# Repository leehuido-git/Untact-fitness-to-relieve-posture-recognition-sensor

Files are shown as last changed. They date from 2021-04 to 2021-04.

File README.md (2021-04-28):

# Untact-fitness-to-relieve-posture-recognition-sensor
Using the MPU-9250 IMU sensor, get the angle of a part of the body and visualize it with Unity or implement the arm shape using the RX-64.
여러개의 MPU-9250 IMU를 통해서 각 신체부위의 quaternion값을 받아 Unity로 시각화, 여러개의 RX-64를 통해서 팔을 구현.

목차
1. [Directory](#Directory)
2. [동기](#동기)
3. [개요](#개요)
4. [Block diagram](#Block-diagram)
5. [Flow chart](#Flow-chart)
6. [Circuit](#Circuit)
7. [Result](#Result)
8. [느낀점](#느낀점)

## Directory
```
.
├── circuit/
    ├── master/
    ├── Robot_Arm/
    ├── slave/
├── datasheet/
├── doc/
    ├── RX-64_정리.hwp
    ├── 중간보고서.hwp
    ├── 결과보고서.hwp
├── img/
├── Modeling/
    ├── stress_calculation/
├── source/
    ├── master/
    ├── Robot_Arm/
    ├── slave/
└── Unity/
```

각각의 것들에 대한 개요입니다:

| 파일 | 설명 |
| --- | --- |
| `RX-64_정리.hwp` | RX-64를 사용하기 위한 스펙, 프로토콜등을 정리 |
| `중간보고서.hwp` | 캡스톤디자인 중간보고서 |
| `결과보고서.hwp` | 캡스톤디자인 결과보고서이며 더 궁금한 내용은 여기를 참조 |
| `master/` | IMU Master를 위한 Arduino 소스 |
| `slave/` | IMU Slave를 위한 Arduino 소스 |
| `Robot_Arm/` | RX-64를 제어하기 위한 Atmel 소스 |

## 동기
1. COVID-19로 인해 비대면  서비스가  증가하는 반면 COVID-19 검체 현장에서는 대면접촉이  이루어 지고 있어 의료관계자들은 감염 위험에 노출되어 있습니다. 또한, 여름에 레벨D 방호복을 입으면 땀 닦을 수도, 물도 마실 수 없어 피부병도 빈번하게 발생하며, 내부 온도는 38도에 육박했다. 그렇기에 저희는 원격으로 COVID-19의 검체를 진행할 수 있다면 이러한 감염위험이나 의료관계자의 불편함을 줄일 수 있을 것입니다. 또한 검체를 채취하는 과정에서 일회용 보호복을 사용하는 경우가 많은데 원격으로 진행할 수 있다면 그 비용을 절약할 수 있을 것입니다.

2. 헬스장의 기존의 대면식 PT를 대체할 비대면식 PT를 제공하며 복잡한 회원 관리가 없어져 일반 헬스장, 아파트 헬스장등 기존 회원 관리의 문제점을 타파할 수 있으며 운동관련 인플루언서들은 자신의 운동을 등록하여 기존의 플랫폼의 단순 동영상 시청의 컨텐츠가 아닌 실제 자신의 운동방식을 알릴 수 있습니다.

## 개요
본 시스템은 크게 4가지 단계로 이루어져 있습니다. (팔 기준)
1. IMU Slave
IMU Slave를 손등, 아래팔, 위팔에 달아주며, 플렉스 센서가 붙여진 장갑을 끼면 각 IMU의 quaternion값, 각 손의 플렉스 센서값을 Wi-Fi를 통해서 IMU Master에게 보내줍니다.
    ```
	동작 알고리즘    
	1. IMU Master으로부터 보정값 받을 때까지 대기한다.
	2. 보정값을 받으면 MPU-9250을 통해 보정된 Quaternion값을 받는다.
    3. Flexible sensor값들을 받는다.
	4. Quaternion값, IMU_2의 이름, Flexible sensor값들을 함께 Wi-Fi를 통해 IMU_MAIN에 전송한다.
    ```

2. IMU Master
초기 IMU Slave가 구동할 때 ACC, MAG, GYRO의 보정값을 IMU Slave에게 보내게 되며, IMU Slave에게 받은 값을 Unity에는 quaternion값을 보내게 되며, Atmega에는 변환된 Euler Angle과 플렉스 센서값을 보내게 됩니다.
    ```
	동작 알고리즘
	1. ACC, MAG, GYRO를 각각 두 번 보정하여 평균값을 계산한다.
	2. Wi-Fi를 통해 5초동안 IMU_1, IMU_2에 보정값 전송한다.
	3. IMU_1, IMU_2...에서 받는 순서대로 Quaternion값을 UART0에 전송한다.
	4. IMU_1, IMU_2에서 받는 순서대로 Quaternion값을 Euler Angle로 계산하고, Flexible sensor값과 함께 UART1을 통해 ATmega에 전송한다.
    ```

3. Atmega-128A(RX-64)
초기 Euler Angle값을 init하여 이후에 변환하는 Euler Angle을 Denavit–Hartenberg parameters를 통해 RX-64에 모터각 전송합니다.
    ```
	동작 알고리즘
	1. IMU_MAIN으로부터 Euler Angle값, Flexible sensor값 받을 때까지 대기한다.
	2. Euler Angle값을 출력하며, 지정된 자세일 때 Button을 눌러 init,
	3. init한 Euler Angle값과의 상대 Euler Angle값을 계산한다.
	4. 상대 Euler Angle값을 Denavit–Hartenberg parameters를 통해 각 motor Angle 계산한다.
	5. Timer를 통해 50ms를 주기로 RX-64에 데이터 전송한다.
	6. Flexible sensor값을 0~180도로 나누어 servomotor PWM 제어한다.
    ```

4. Unity
받은 quaternion값을 통해서 초기 Quaternion값을 init하여 이후에 변환하는 상대 Quaternion값을 계산하여 Bone을 제어합니다.
    ```
	동작 알고리즘
	1. UART를 사용할 PORT 설정 및 연다.
	2. IMU_MAIN으로부터 Quaternion값 받을 때까지 대기한다.
	3. Quaternion값을 출력하며, 지정된 자세일 때 spacebar를 눌러 init.
	4. init한 Quaternion값과의 상대 Quaternion값을 계산한다.
	5. Bone제어한다.
    ```

## Block diagram
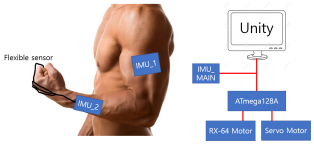
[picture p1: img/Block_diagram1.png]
Block_diagram1
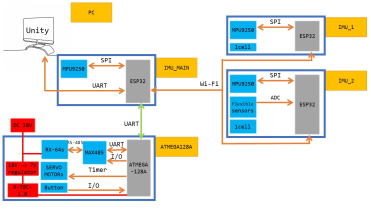
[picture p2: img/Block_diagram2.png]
Block_diagram2
 
* 부하가 많이 발생하여 RX-64 maximun voltage에 근접하는 18v인가
* R-78C 5.0-1.0을 통해서 atmega128A recommended voltage인 5v로 switching regulation
* RX-64는 RS-485통신을 사용하므로 max485를 통해서 RS-232(UART)를 RS-485로 변환
* Atmega와 IMU간 UART 송수신
* Computer와 IMU간 UART 송수신
* IMU인 MPU-9250과 MCU인 ESP32간 I2C, SPI통신을 사용할 수 있는데 빠른 SPI통신 사용(I2C at 400kHz or SPI at 1MHz)
* IMU Slave는 배터리 1cell을 사용, 통신은 Wi-Fi을 사용하여 무선으로 사용 가능

## Flow chart
**1. IMU Master flow chart**  
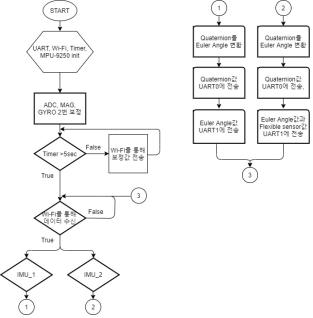
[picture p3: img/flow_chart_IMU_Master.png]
flow_chart_IMU_Master
  

**2. IMU Slave flow chart**  
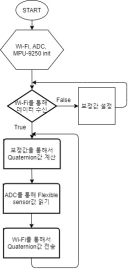
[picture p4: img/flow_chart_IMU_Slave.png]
flow_chart_IMU_Slave


**3. Atmega flow chart**  
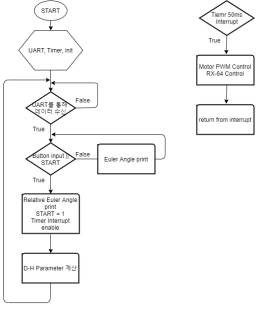
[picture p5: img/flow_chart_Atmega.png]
flow_chart_Atmega


## Circuit
**1. IMU Master Circuit**  
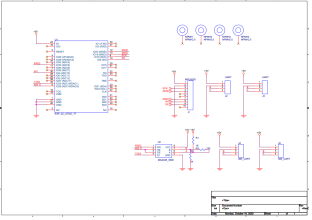
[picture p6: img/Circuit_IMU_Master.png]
Circuit_IMU_Master
  

**2. IMU Slave Circuit**  
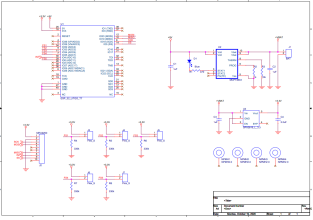
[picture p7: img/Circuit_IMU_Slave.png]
Circuit_IMU_Slave


**3. Atmega Circuit**  
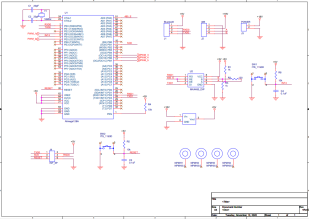
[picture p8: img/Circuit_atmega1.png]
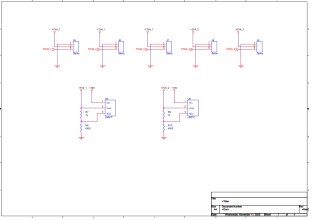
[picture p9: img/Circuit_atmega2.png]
 

## Result
result1  
실제 프로토타입으로 개발하였던 센서를 기반으로 atmega와 연동하여 RX-64를 구동하는 것을 보여줍니다.

result2  
실제 프로토타입으로 개발하였던 센서를 기반으로 Unity와 연동하여 스마트미러를 통해 데이터를 받아오는 것을 보여줍니다.

## 느낀점
1. 현재 COVID-19가 창궐하면서 언택트 시대에서 온택트 시대로 넘어가고 있습니다. 온택트 시대는 온라인을 통해 대면을 하는 것으로 소비자들의 간접적 경험을 심어줄 수 있는 체험 미디어가 있느냐 없느냐인데, 저희가 만든 로봇팔과 같이 소비자에게 행동을 보여줌으로써 간접적 경험을 심어줄 수 있습니다. 또한 이뿐만 아니라 공장 내 작업자의 협동로봇 간편 티칭으로도 사용할 수 있습니다. 4차 산업혁명의 주요 과제로 근로자와 함께 근로공간을 공유하여 사용하는 사례가 많은데 협동로봇을 제어에는 전문가가 투입되지만 본 솔루션을 통해 작업자의 신체에 센서를 부착하여 원격으로 작업을 수행할 수 있을 것입니다.
2. IMU를 통해서 로봇 팔을 제작, 제어하는데에는 많은 분야의 지식이 필요하고 생각보다 잘 안된게 아쉽습니다.
3. 로봇 팔의 모터를 더 강력한 모터를 사용, 모터를 추가하여 자유도를 높이고 싶지만 자원의 제약으로 사용하지 못하는게 아쉽습니다.
4. Magwick Filter와 보정을 모두 했지만 오차가 존재하며 특히 Yaw값의 누적오차가 발생했습니다.
4. 생각외로 servomotor는 전류소모가 매우 크다는 것을 알게 되었습니다.

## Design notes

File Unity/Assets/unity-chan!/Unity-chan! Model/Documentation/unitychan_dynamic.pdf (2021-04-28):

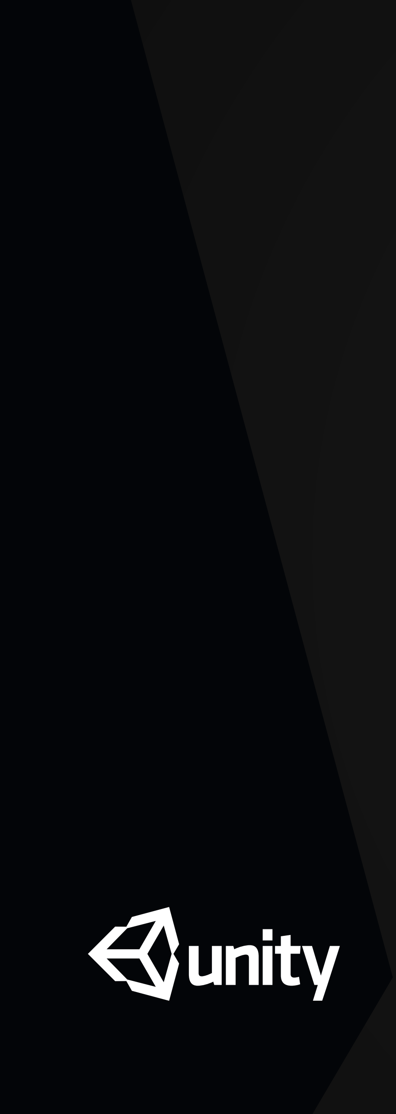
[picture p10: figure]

# ダイナミック版ユニティちゃん （unitychan_dynamic） マニュアル

# Unity4.3.4以上対応

2014/07/23

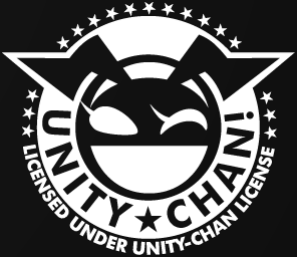
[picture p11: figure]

# 『ダイナミック版ユニティちゃん』とは

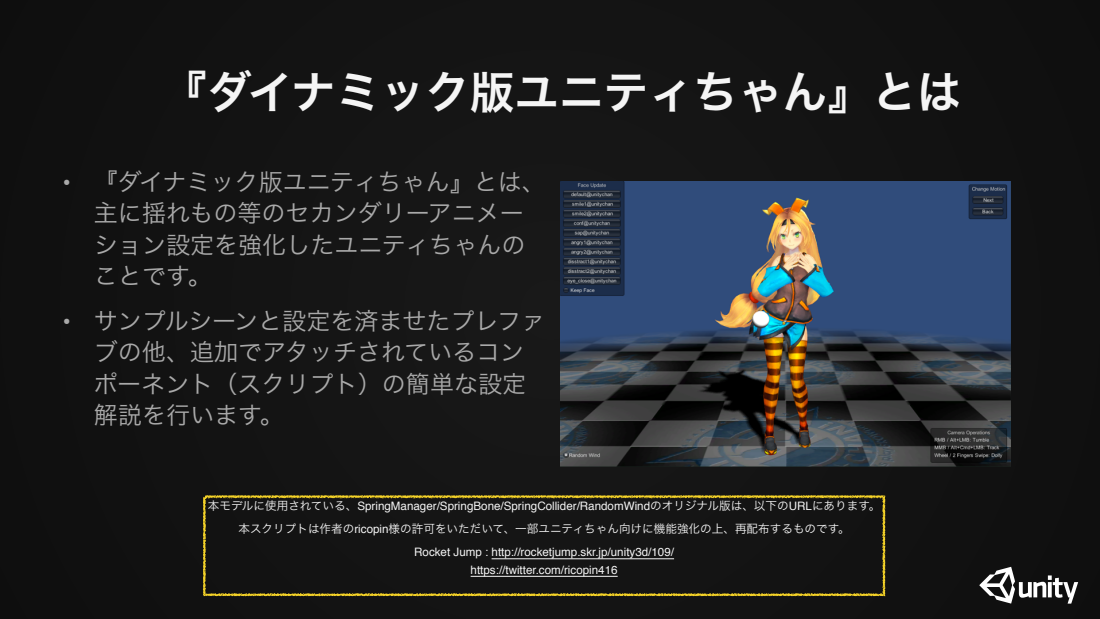
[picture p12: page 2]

• 『ダイナミック版ユニティちゃん』とは、
主に揺れもの等のセカンダリーアニメー
ション設定を強化したユニティちゃんの
ことです。
• サンプルシーンと設定を済ませたプレファ
ブの他、追加でアタッチされているコン
ポーネント（スクリプト）の簡単な設定
解説を行います。

本モデルに使用されている、SpringManager/SpringBone/SpringCollider/RandomWindのオリジナル版は、以下のURLにあります。

本スクリプトは作者のricopin様の許可をいただいて、一部ユニティちゃん向けに機能強化の上、再配布するものです。

Rocket Jump : http://rocketjump.skr.jp/unity3d/109/

https://twitter.com/ricopin416

# サンプルシーン SecondaryAnimation Locomotion

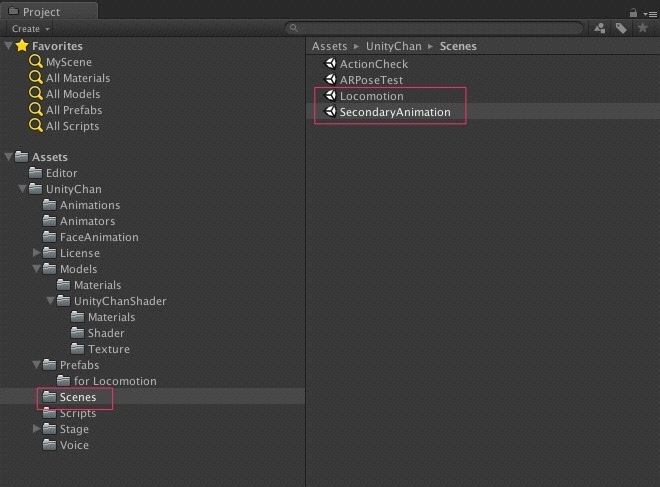
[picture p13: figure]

### - Assets>UnityChan>Scenes中の 「SecondaryAnimation」と「Locomotion」がサ ンプルシーンになります。

### - SecondaryAnimationは、ポージングやダンス モーションなど、ユニティちゃんが原点の付近で あまり動かない場合のセッティング例です。見栄 え優先で揺れ物を揺らすセッティングになってい

ます。

### - Locomotionは、ユニティちゃんを PlayerControllerなどで動かす場合のセッティン グ例です。揺れ物のセッティングが少し固めになっ ています。

### - 各シーンを開くことで、すぐにダイナミック設定 のついたユニティちゃんで遊ぶことができます。

# プレファブ unitychan_dynamic unitychan_dynamic_locomotion

### - Prefabsフォルダ内には、サンプルシーンで使用されて

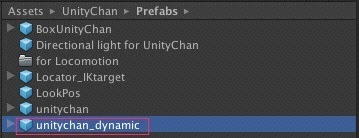
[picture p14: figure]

### いるダイナミック版ユニティちゃんのプレファブが入っ ています。

### - Assets>UnityChan>Prefabs unitychan_dynamic →SecondaryAnimationシーン用プレファブ

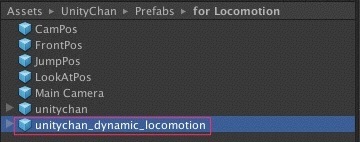
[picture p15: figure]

### - Assets>UnityChan>Prefabs>for Locomotion unitychan_dynamic_locomotion →Locomotionシーン用プレファブ

### - これらのプレファブを自分の好きなシーンに配置する ことで、各ダイナミック用設定を済ませたユニティちゃ んをすぐに使うことができるようになります。

# 『ダイナミック版ユニティちゃん』の 揺れ物制御用コンポーネントについて

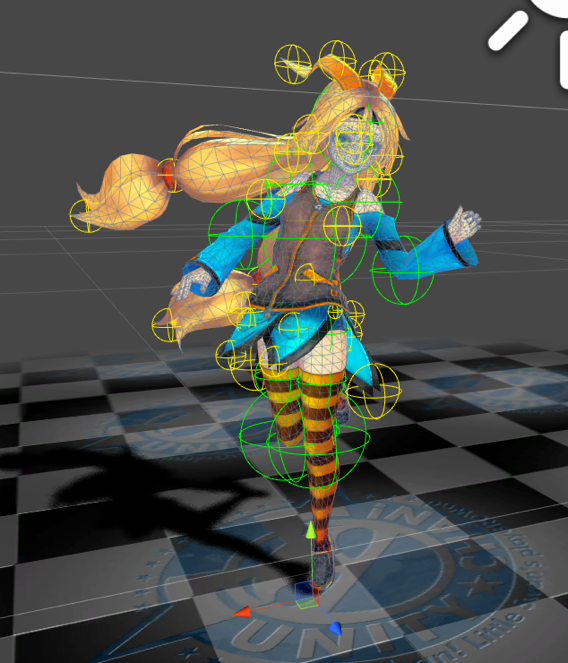
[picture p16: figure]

- 『ダイナミック版ユニティちゃん』の揺れ物制御用のコンポーネントは以 下のような構成になっています。
- SpringManager.cs：SpringBoneを制御するマネージャー。ユニティちゃ ん本体にアタッチされる。
- SpringBone.cs：各揺れ物用ボーンにアタッチされるコンポーネント。揺 れ物に設定されている各ボーン（ジョイント）にアタッチされる
- SpringCollider.cs：SpringBone専用の当たり判定用コライダー。当たり判 定を付けたいジョイントやロケータにアタッチされる。
- RandomWind.cs：ランダムに風にそよぐような効果を生み出すコンポー ネント。ユニティちゃん本体にアタッチされる。ゲームビュー内の 「Random Wind」で機能をON/OFFできる。
- CreateLocatorHere.cs：SpringCollider設定支援用エディタ拡張ツール。 Hierarchy上であるジョイントを指定して実行することで、そのジョイント の子の位置にロケータを生成できる。ロケータは親のジョイントからロー カル移動をすることで、位置をオフセットすることができる。生成したロ ケータにはSpringCollider.csをアタッチする。

# 『ダイナミック版ユニティちゃん』に 追加されたその他のコンポーネント について

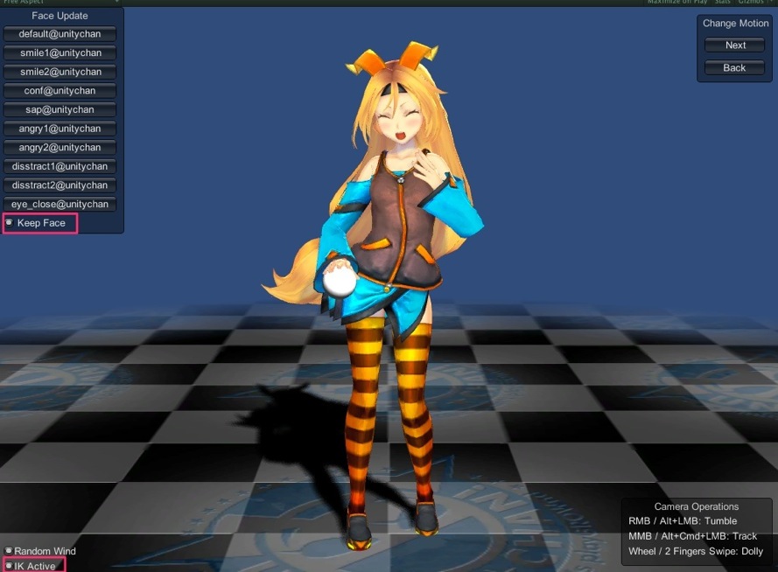
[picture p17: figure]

- AutoBlink.cs：自動で目パチアニメーションをさせ るコンポーネント。
- FaceUpdate.cs：機能強化版。表情の固定ができる ようになった（KeepFaceをチェック後、表情スイッ チを押す）他、Mecanimアニメーションイベント
で、OnCallFaceChange(“表情名”)を呼び出すこと で、各アニメーションデータ上で、タイムラインに
沿って表情変化を設定できます。
- IKCtrlRightHand.cs：Pro Onlyの機能。右手のIKコ ントロールのサンプルです。コンポーネントを有効
にした後、ゲームビュー内の「IK Active」でON/OFF できます。

# SpringBone.csの設定①

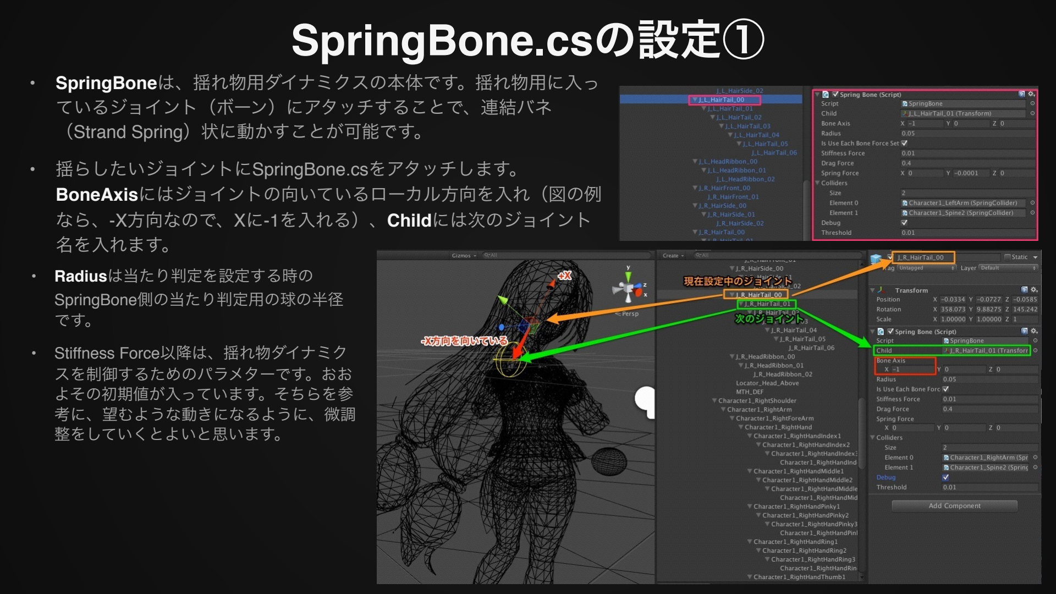
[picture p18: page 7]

### - SpringBoneは、揺れ物用ダイナミクスの本体です。揺れ物用に入っ ているジョイント（ボーン）にアタッチすることで、連結バネ （Strand Spring）状に動かすことが可能です。

### - 揺らしたいジョイントにSpringBone.csをアタッチします。 BoneAxisにはジョイントの向いているローカル方向を入れ（図の例 なら、-X方向なので、Xに-1を入れる）、Childには次のジョイント 名を入れます。

- Radiusは当たり判定を設定する時の
SpringBone側の当たり判定用の球の半径
です。
- Stiffness Force以降は、揺れ物ダイナミク スを制御するためのパラメターです。おお
よその初期値が入っています。そちらを参
考に、望むような動きになるように、微調
整をしていくとよいと思います。

# SpringBone.csの設定②

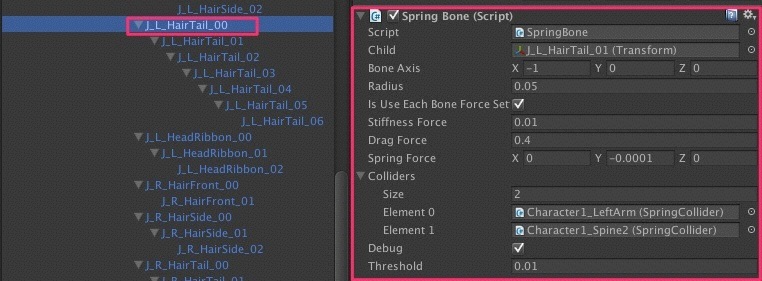
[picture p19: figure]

- StiffnessForce、DragForceはそれぞれ「バネが戻るフォース」「フォースの 減衰力」です。後に説明しますが、IsUseEachBoneForceSetにチェックが 入っている時には、SpringBone側に設定されているこれらのパラメターが使用 されます。
- Collidersには、各SpringBoneコンポーネントと当たり判定を設定したい SpringColliderを設定します。
- 最後にThresholdは、このSpringBoneコンポーネントを制御している SpringManager側のDynamicRatioが有効になる最低値を設定します。（この値 を上げることで、一部のSpringBoneを個別に停止して、揺れ物ボーンに元々つ いているアニメーションに切り替えることが可能になります。）
- SpringBoneの設定で重要なのは、①でのChild/BoneAxis/Radiusの設定と、②の Collidersの設定です。その他の値は、初期値を参考に微調整をするとよいで しょう。
- SpringBoneの効き具合の調整は、上のStiffnessForce/DragForceの値で微調 整をする他に、後述するSpringManager側のDynamicRatioで効果自体の効き 具合を調整してしまうという方法があります。大体の設定が終わった後は、 DynamicRatio側で使う状況に合わせて調整するほうが便利なようです。

# SpringManager.csの設定

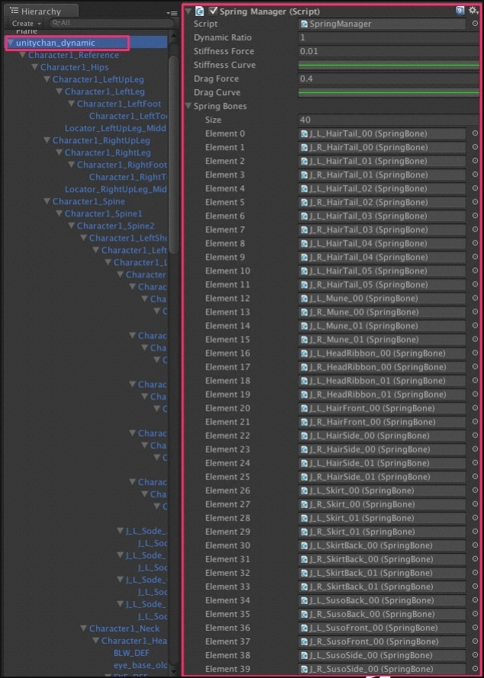
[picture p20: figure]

- SpringManagerは、配下にあるSpringBoneを制御するコンポーネントです。
- SpringBones以下に管理させたいSpringBoneがアタッチされているジョイントを必ず親 から順に指定します。
- DynamicRatioは、配下にあるSpringBoneの影響の強さを制御するパラメターです。 DynamicRatio=1の時、SpringBoneの影響が最大になり、DynamicRatio=0の時、 SpringBoneの機能はキャンセルされます。その場合、ジョイントが持っている元々の ローカルローテーション値もしくは、揺れ物ボーンに付けられているアニメーションで のローテーション値が使用されます。DynamicRatioは、各SpringBoneに設定できる Thresholdを参照できますので、各SpringBoneのThresholdを適宜設定し、DynamicRatio を調整することで、一部の揺れ物ボーンは、元々のアニメーションで、一部の揺れ物ボー ンはSpringBoneで動かすというようなことも可能です。
- SpringManager側にあるStiffnessForceとDragForceは、配下にあるSpringBoneの同名の 値の最適値を探るために使えます。有効にする場合には、各SpringBoneの IsUseEachBoneForceSetがオフになっている必要があります。カーブなどを利用して 様々な設定のパターンを探ることができるようになっています。SpringManager上でシ ミュレーションした値は、エディタ上でしか使えませんので、よい値が見つかったら SpringBone側に値をコピーし、IsUseEachBoneForceSetをチェックすることをお薦めし ます。
- なおSpringManagerは、各揺れ物ボーンのチェインの一番上の階層に付けることで、各 揺れ物ボーンのチェインを個別に管理することも可能です。

# SpringCollider.csの設定

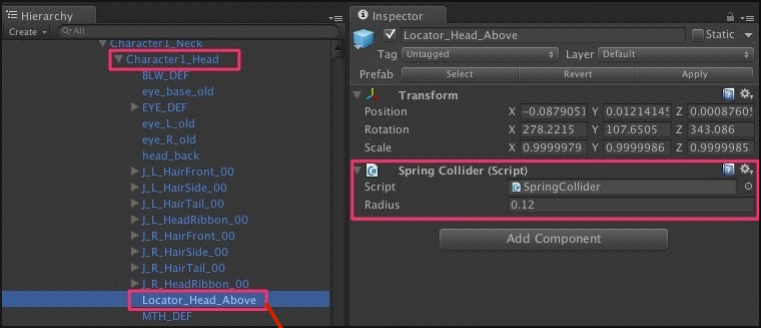
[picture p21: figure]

- SpringColliderは、SpringBoneコンポーネントと衝突判定を行うためのコンポーネン トです。ジョイントやジョイントからオフセットした位置に設定したロケータにアタッ チすることで、当たり判定用のスフィアコライダーとして利用することができます。 Radiusが当たり判定用のスフィアコライダーの半径となります。
- 当たり判定をとりたいSpringBoneコンポーネント側の配列（Colliders）に、判定し たいSpringColliderをアタッチしたオブジェクト名を指定します。
- エディタ拡張コマンドCreateLocatorHere.csを使うことで、Hierarchy上でジョイント の子の位置にロケータを生成できます。ロケータは親のジョイントからローカル移動を することで、位置をオフセットすることができますので、オフセットした位置で SpringColliderを複数設定することで、複雑な当たり判定領域を設定したり、ジョイン トから離れている位置に当たり判定領域を設定することができます。 CreateLocatorHereは、Hierarchy上でジョイントを選んだ後、GameObjectメニューか らコマンド選択する他、Transformコンポーネント上で右クリックメニューから呼び出 すことで利用できます。

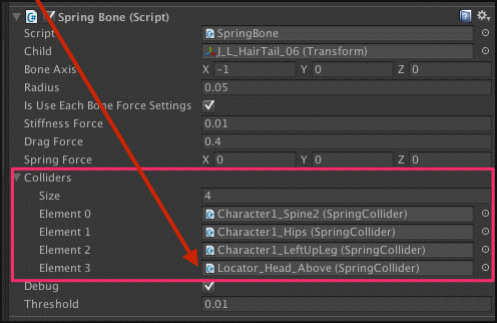
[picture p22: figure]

- SpringColliderはUnity標準の物理エンジンによる当たり判定を使用していませんので、 ご注意ください。

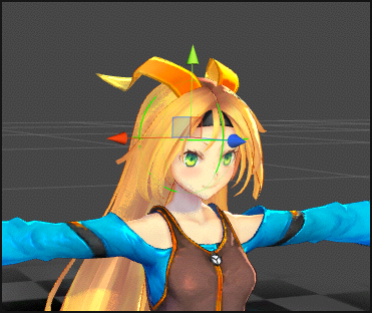
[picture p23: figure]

# FaceUpdate.cs / OnCallFaceChangeの設定

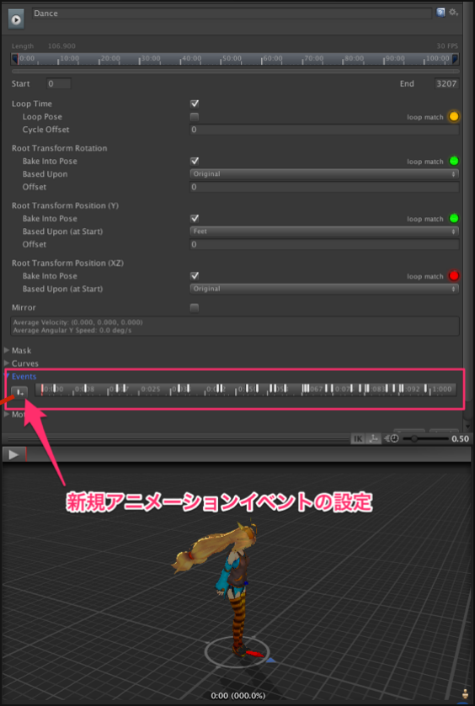
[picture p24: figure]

- FaceUpdate.cs：機能強化版。表情の固定ができるようになった （KeepFaceをチェック後、表情スイッチを押す）他、Mecanimアニメー ションイベントで、OnCallFaceChange(“表情名”)を呼び出すことで、各ア ニメーションデータ上で、タイムラインに沿って表情変化を設定できます。
- ダンスモーションなどのアニメーションデータをMecanimで開き、Events タブを開いて、モーションに合わせて新規アニメーションイベントを設定し ます。
- Edit AnimationEventウィンドウが開きますので、Functionに 「OnCallChangeFace」と入れ、Stringに「変更したいフェイスの名前」を 指定します。

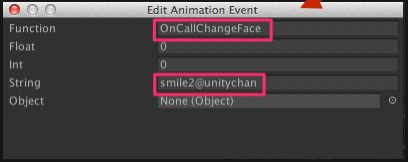
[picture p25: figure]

# FaceUpdate.cs / 新規表情の追加

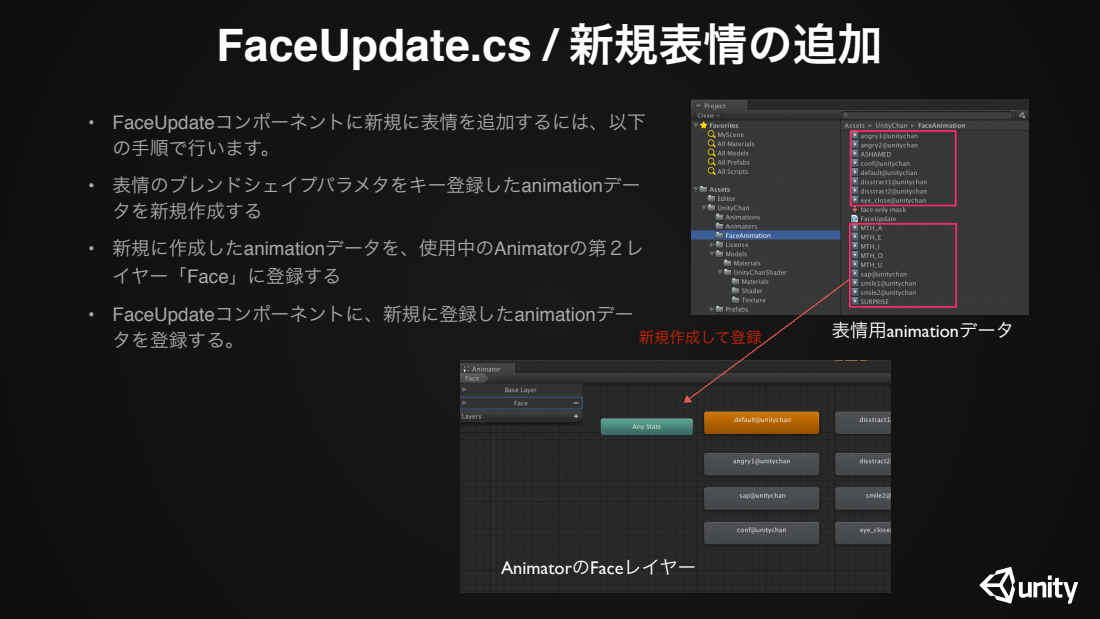
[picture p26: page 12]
• FaceUpdateコンポーネントに新規に表情を追加するには、以下 の手順で行います。; • 表情のブレンドシェイプパラメタをキー登録したanimationデー タを新規作成する; • FaceUpdateコンポーネントに、新規に登録したanimationデー; タを登録する。; 表情用animationデータ; AnimatorのFaceレイヤー; 新規作成して登録

• 新規に作成したanimationデータを、使用中のAnimatorの第２レ
イヤー「Face」に登録する

# 表情アニメーションデータの新規作成

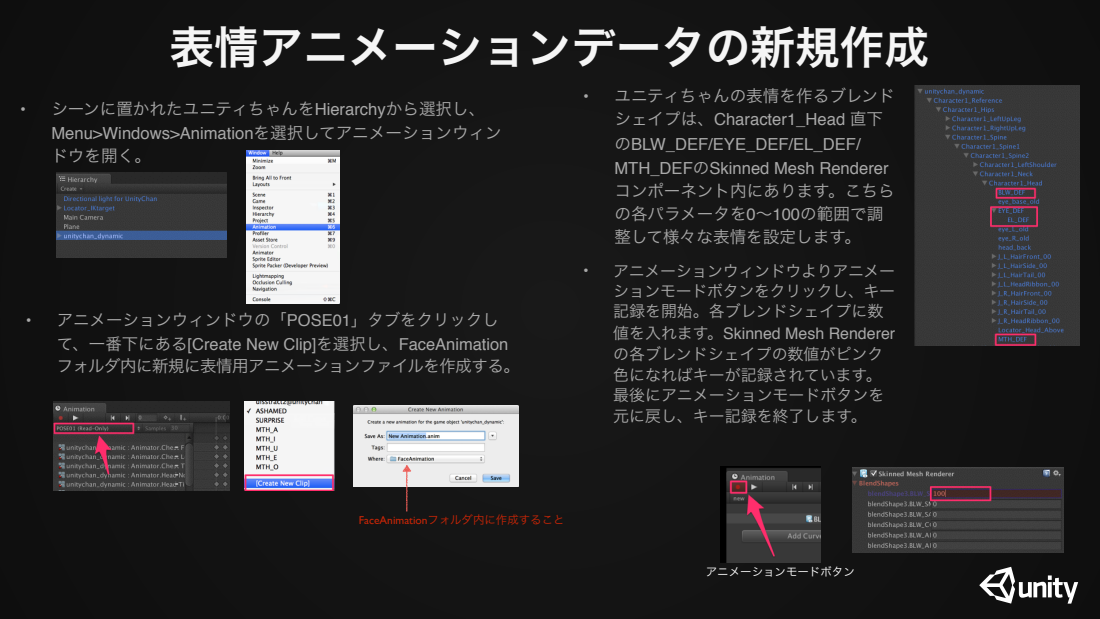
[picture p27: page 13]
• ユニティちゃんの表情を作るブレンド シェイプは、Character1_Head 直下 のBLW_DEF/EYE_DEF/EL_DEF/ MTH_DEFのSkinned Mesh Renderer コンポーネント内にあります。こちら の各パラメータを0～100の範囲で調 整して様々な表情を設定します。; アニメーションモードボタン; FaceAnimationフォルダ内に作成すること

• シーンに置かれたユニティちゃんをHierarchyから選択し、
Menu>Windows>Animationを選択してアニメーションウィン
ドウを開く。

• アニメーションウィンドウよりアニメー
ションモードボタンをクリックし、キー
記録を開始。各ブレンドシェイプに数
値を入れます。Skinned Mesh Renderer
の各ブレンドシェイプの数値がピンク
色になればキーが記録されています。
最後にアニメーションモードボタンを
元に戻し、キー記録を終了します。

• アニメーションウィンドウの「POSE01」タブをクリックし
て、一番下にある[Create New Clip]を選択し、FaceAnimation
フォルダ内に新規に表情用アニメーションファイルを作成する。

# 表情アニメーションデータの登録

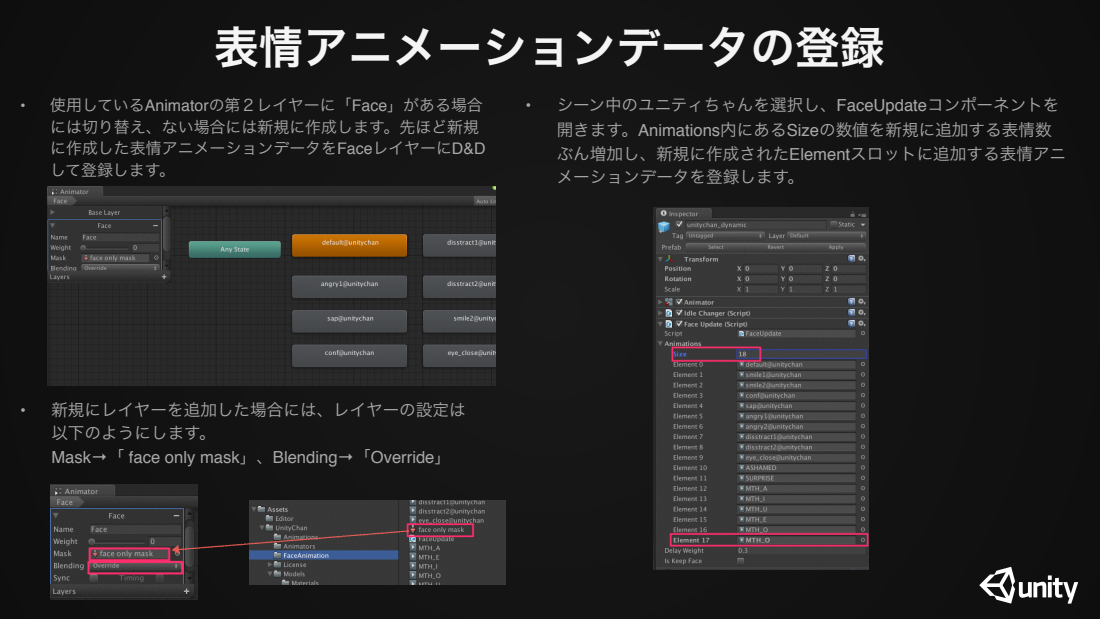
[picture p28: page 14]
• シーン中のユニティちゃんを選択し、FaceUpdateコンポーネントを 開きます。Animations内にあるSizeの数値を新規に追加する表情数 ぶん増加し、新規に作成されたElementスロットに追加する表情アニ メーションデータを登録します。

• 使用しているAnimatorの第２レイヤーに「Face」がある場合
には切り替え、ない場合には新規に作成します。先ほど新規
に作成した表情アニメーションデータをFaceレイヤーにD&D
して登録します。

• 新規にレイヤーを追加した場合には、レイヤーの設定は
以下のようにします。
Mask→「 face only mask」、Blending→「Override」

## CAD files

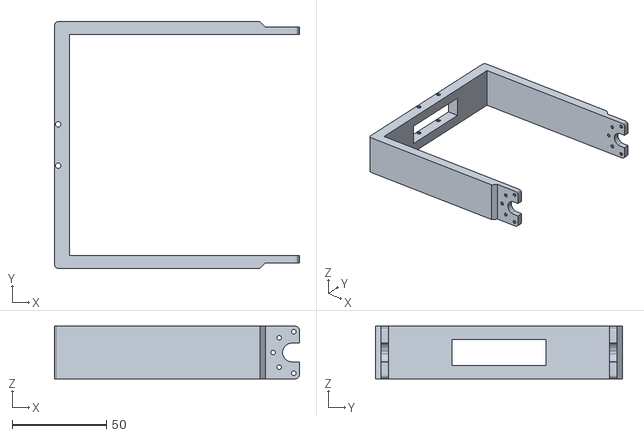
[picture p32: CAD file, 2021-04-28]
Modeling/shoulder_gear.stl
130.0 x 131.0 x 28.0

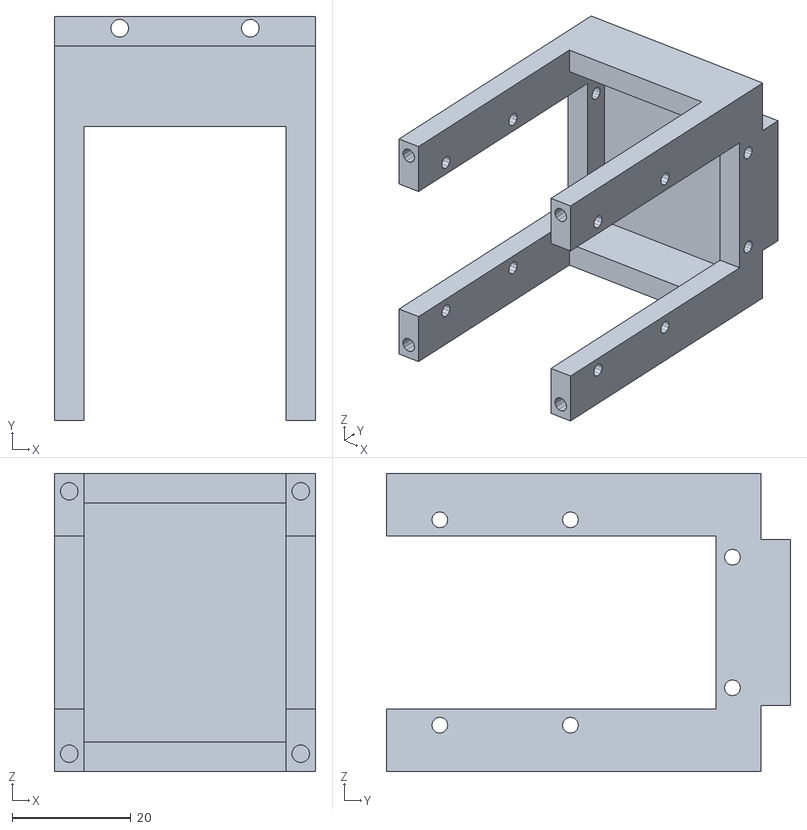
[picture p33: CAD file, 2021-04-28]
Modeling/elbow.stl
44.0 x 68.1 x 50.2

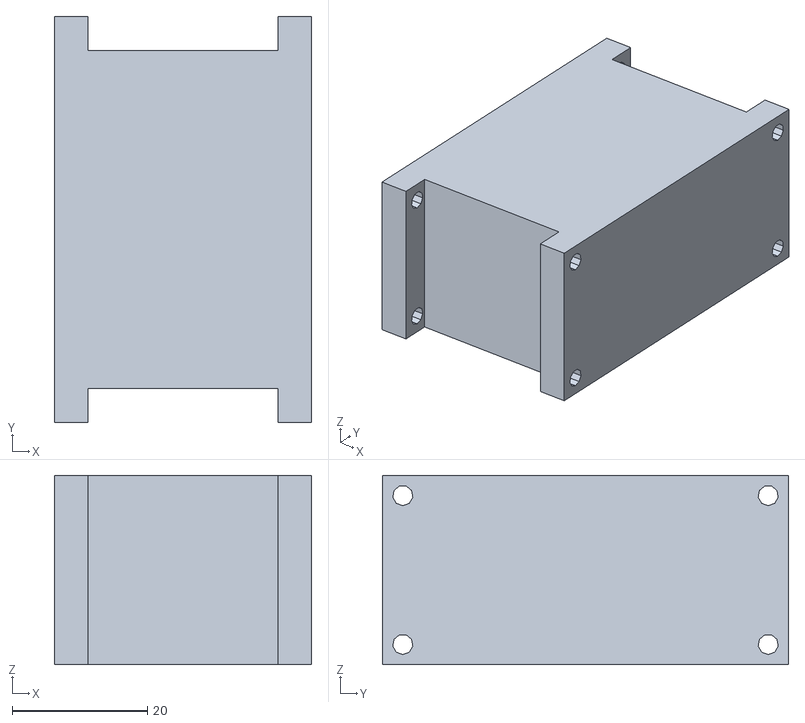
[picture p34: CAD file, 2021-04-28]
Modeling/upperarm.stl
38.0 x 60.0 x 28.0

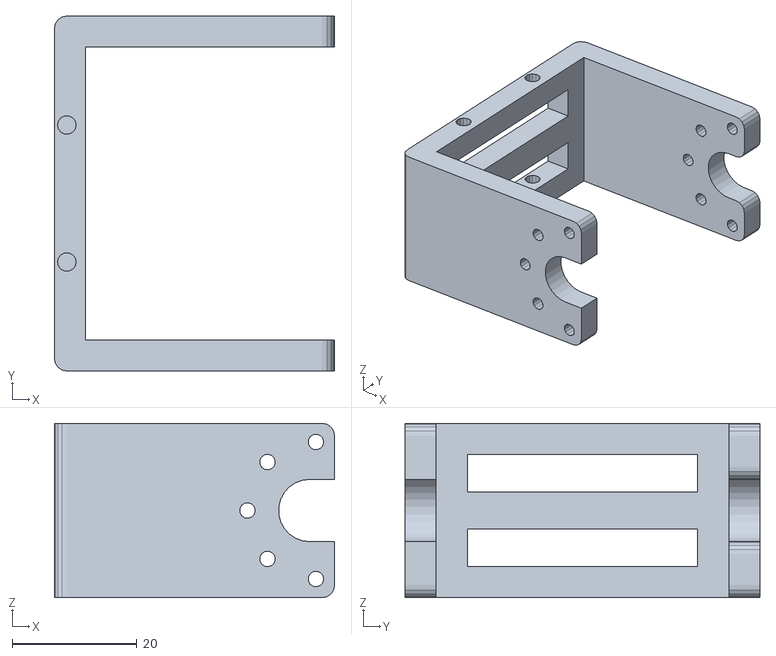
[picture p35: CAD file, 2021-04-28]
Modeling/elbow_gear.stl
45.0 x 57.0 x 28.0

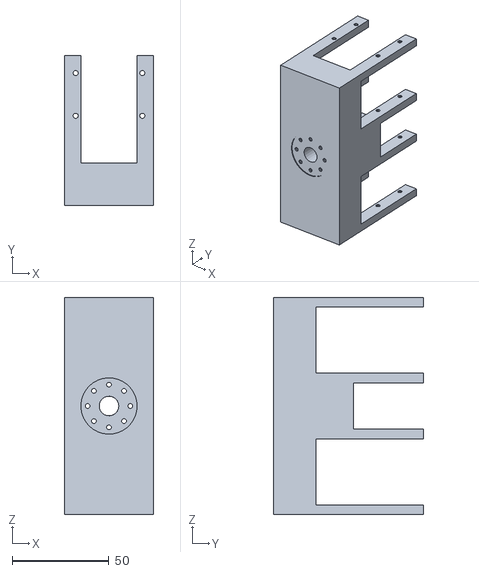
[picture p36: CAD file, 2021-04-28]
Modeling/shoulder.stl
46.0 x 77.2 x 112.0

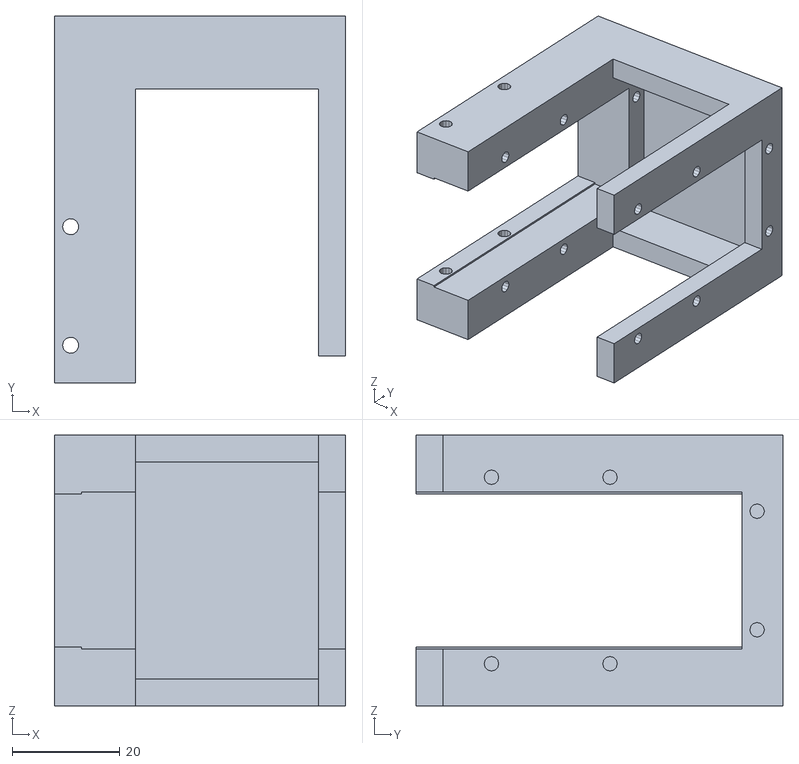
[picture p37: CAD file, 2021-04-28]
Modeling/elbow_fore.stl
54.0 x 68.1 x 50.2

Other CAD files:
Modeling/elbow.ipt
Modeling/elbow_fore.ipt
Modeling/elbow_gear.ipt
Modeling/shoulder.ipt
Modeling/shoulder_gear.ipt
Modeling/stress_calculation/3030500.ipt
Modeling/stress_calculation/3030600.ipt
Modeling/stress_calculation/3030800.ipt
Modeling/stress_calculation/3060400.ipt
Modeling/stress_calculation/부품1.ipt
Modeling/stress_calculation/조립품1.iam
Modeling/upperarm.ipt

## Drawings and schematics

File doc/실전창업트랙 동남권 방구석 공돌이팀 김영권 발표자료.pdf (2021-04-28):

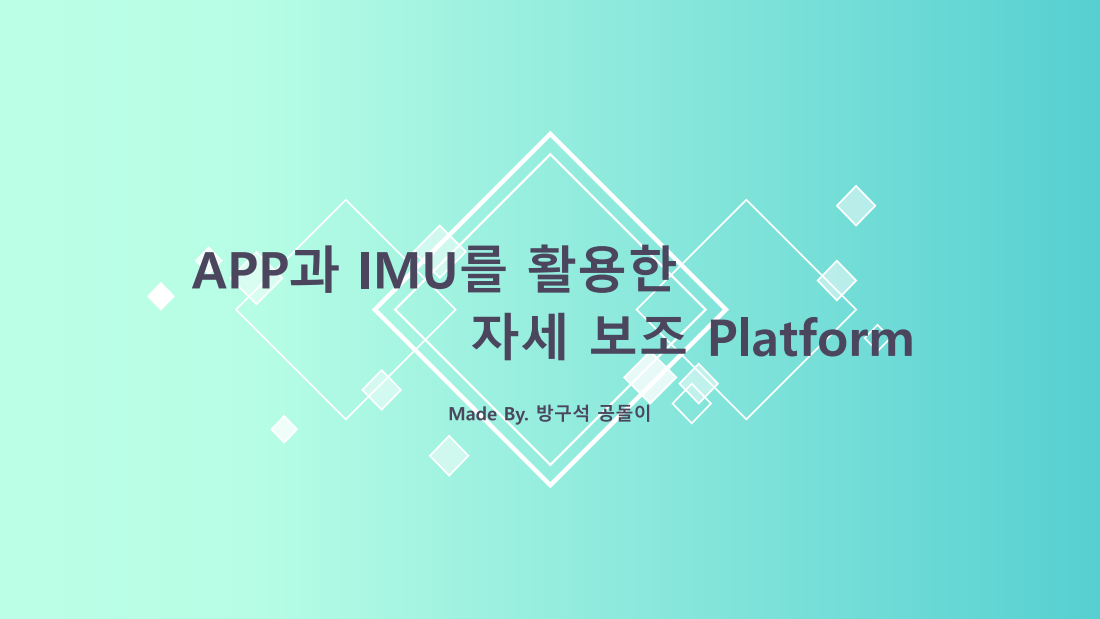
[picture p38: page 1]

APP과 IMU를 활용한

자세 보조 Platform

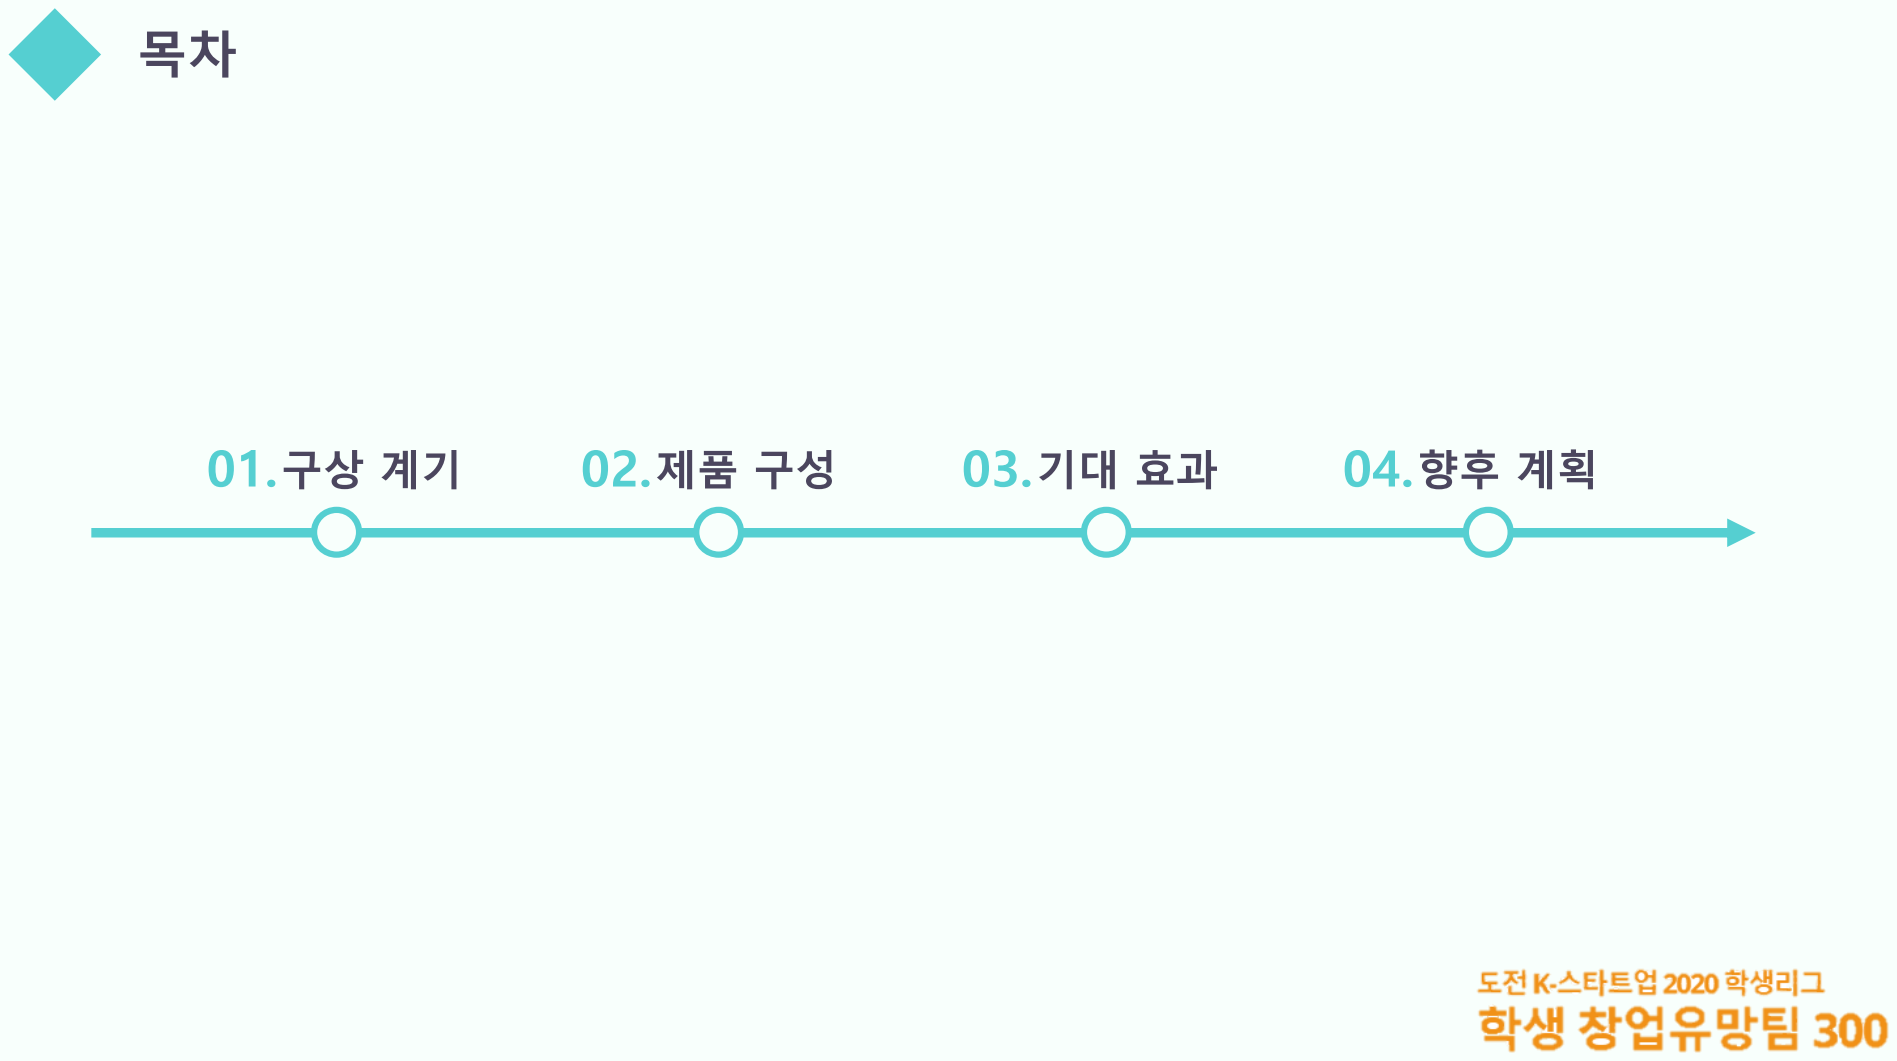
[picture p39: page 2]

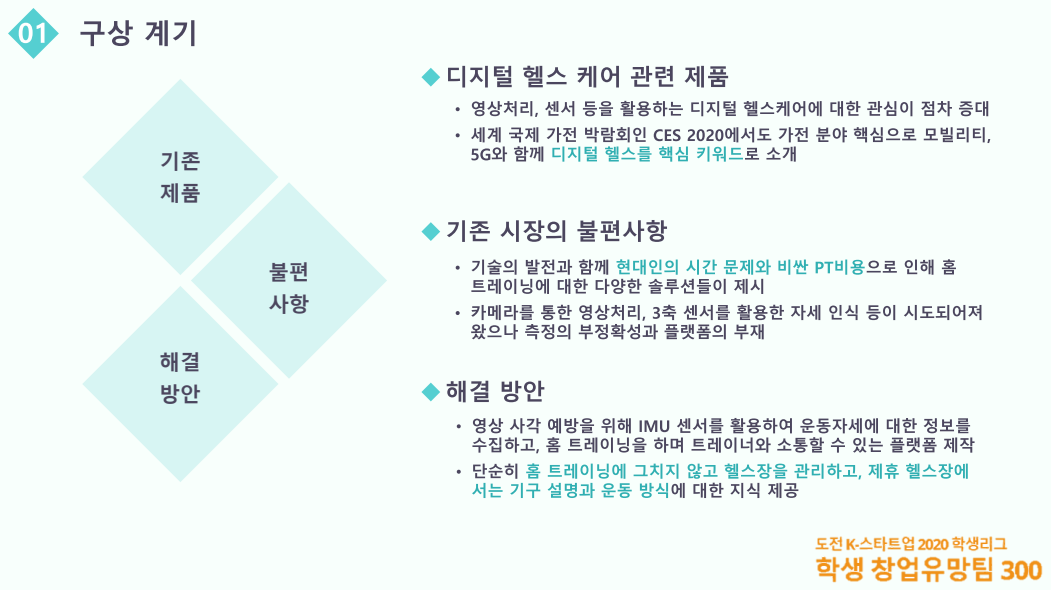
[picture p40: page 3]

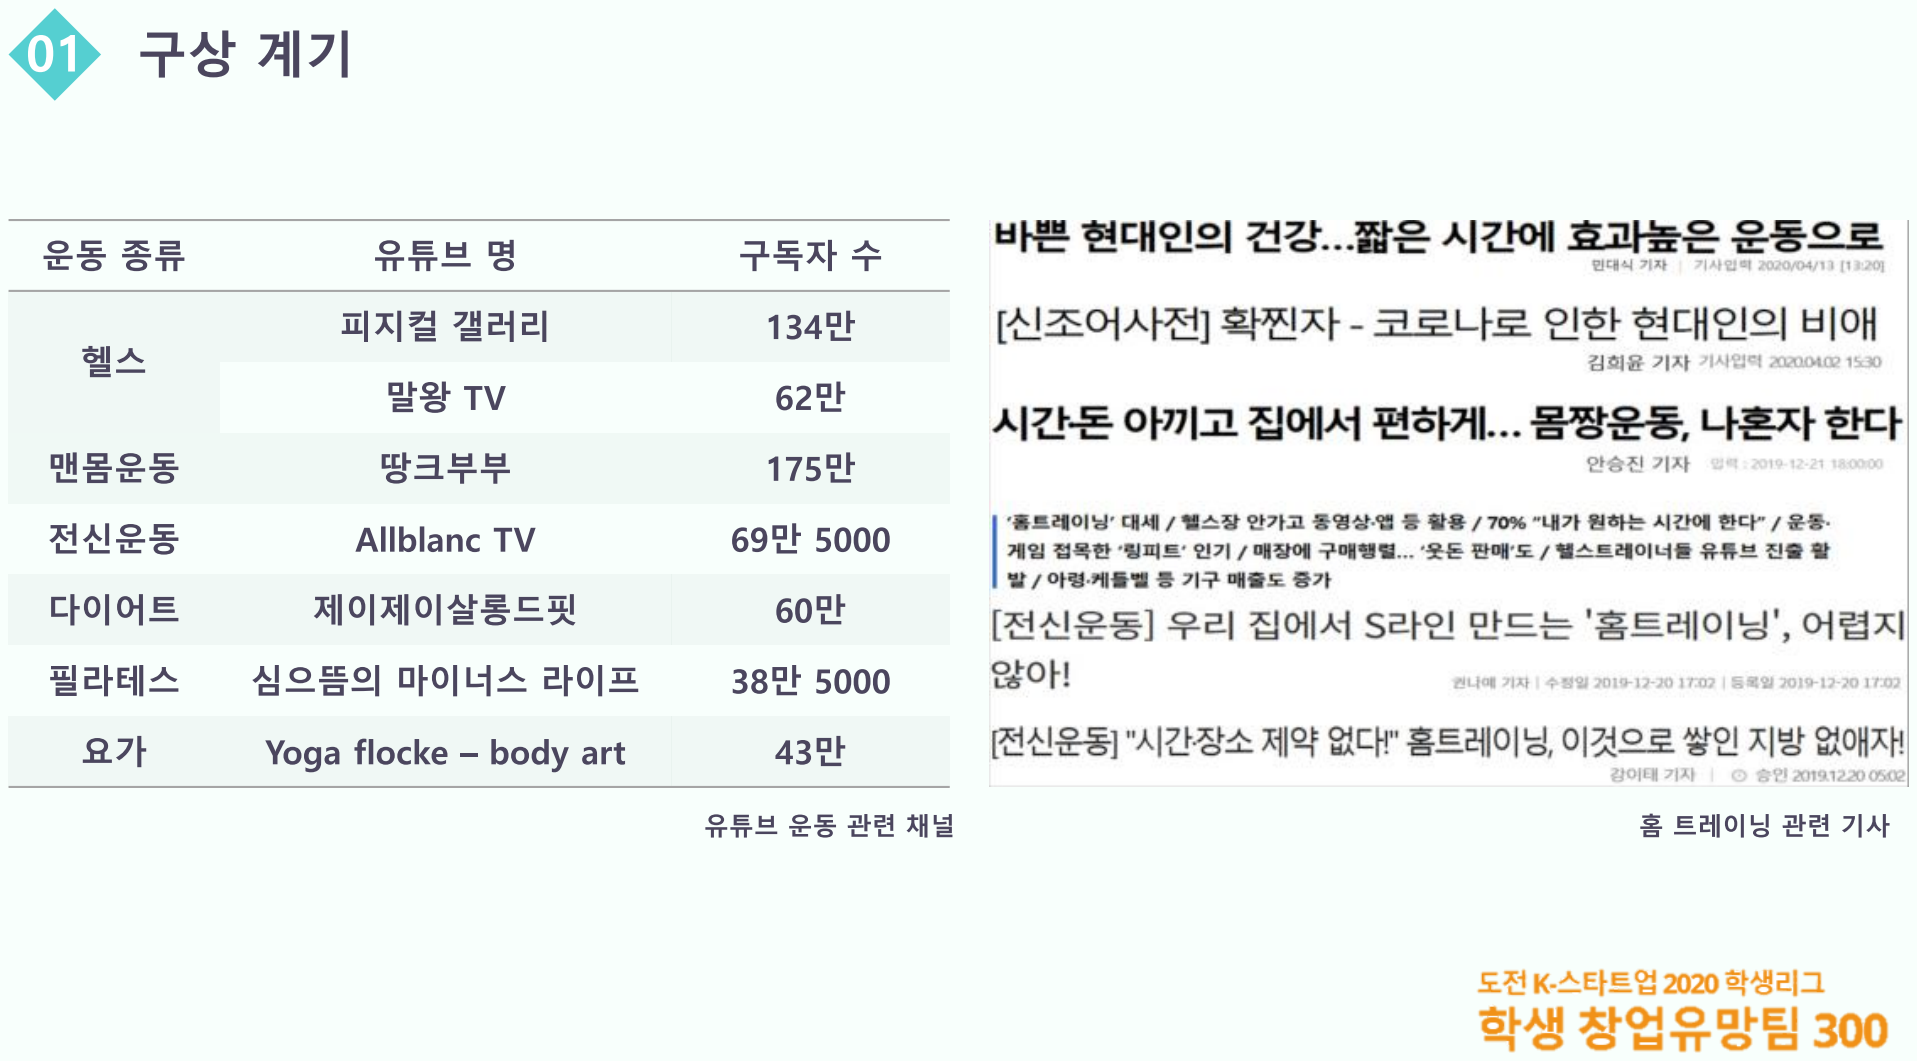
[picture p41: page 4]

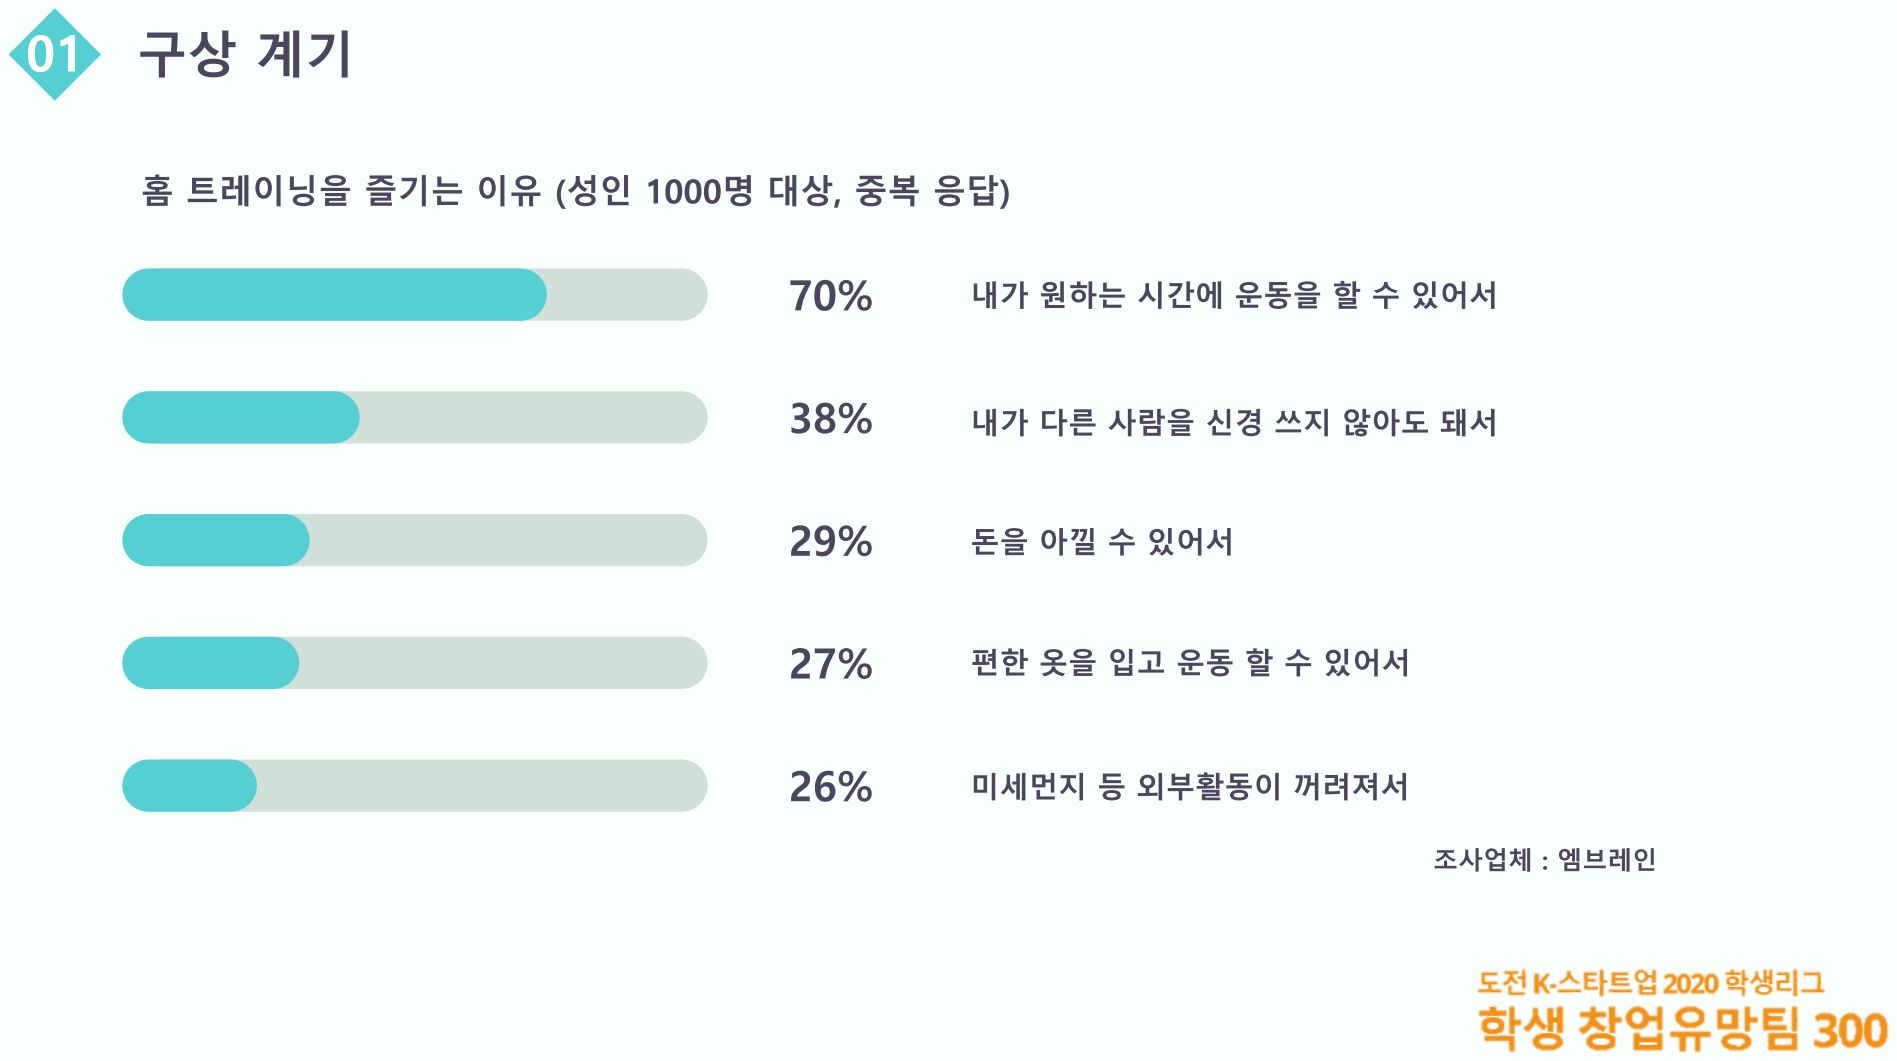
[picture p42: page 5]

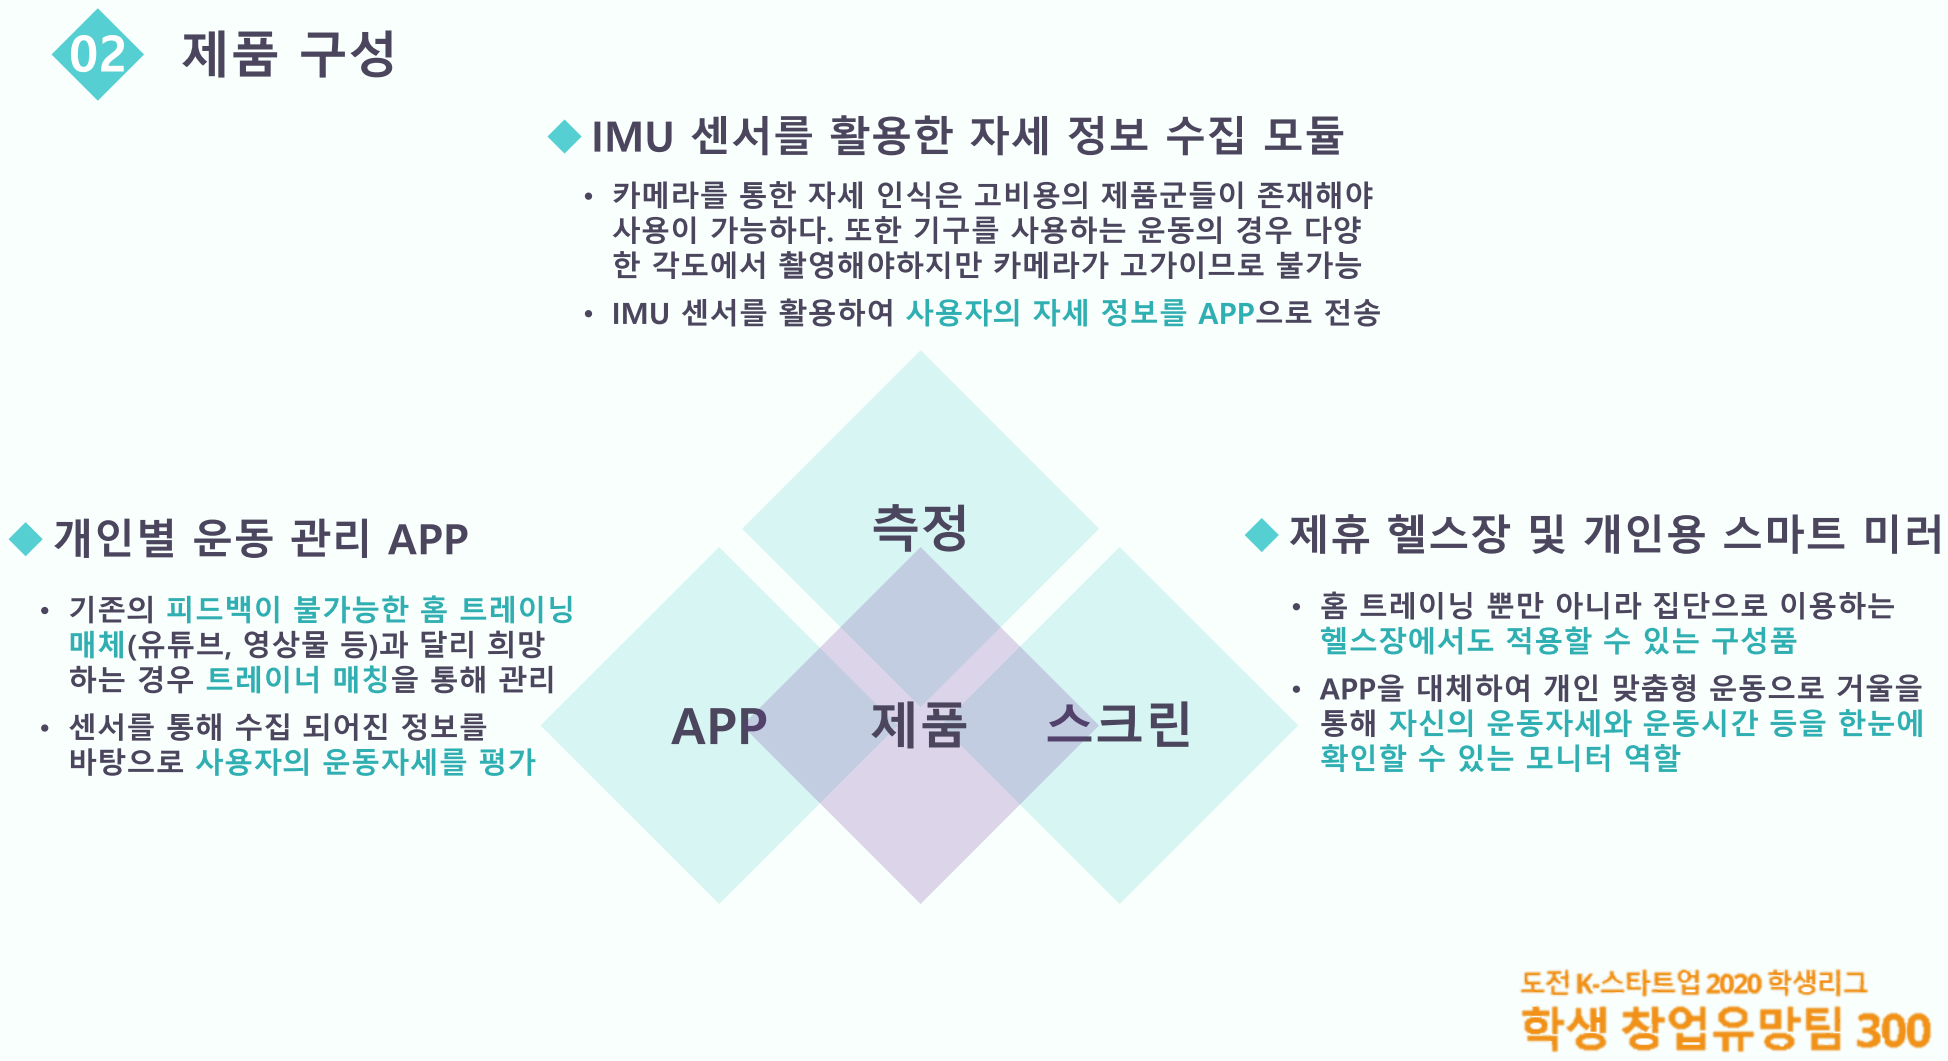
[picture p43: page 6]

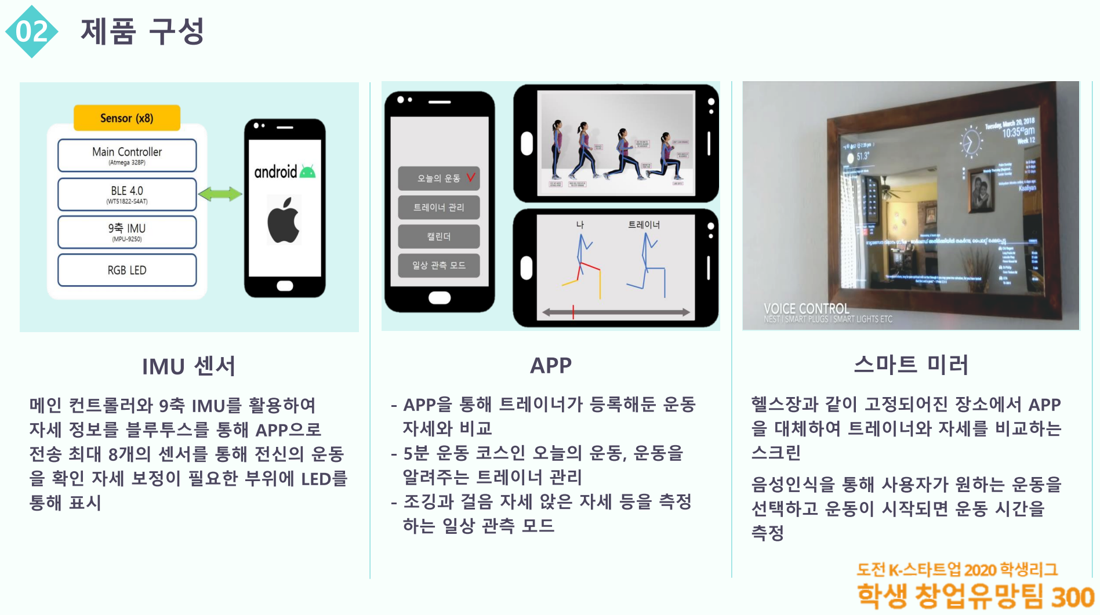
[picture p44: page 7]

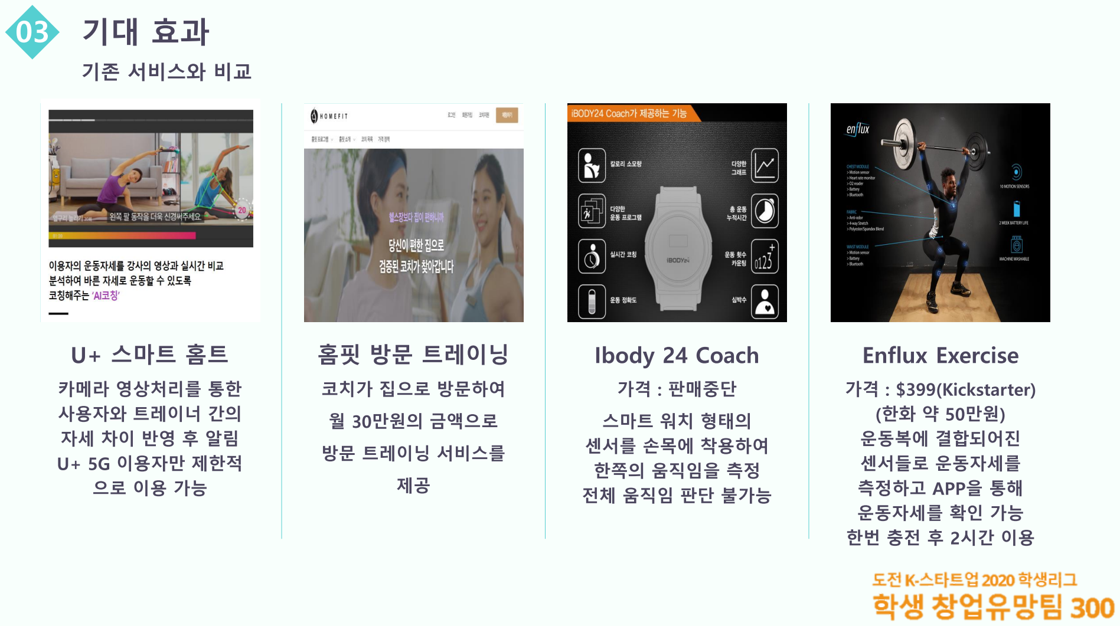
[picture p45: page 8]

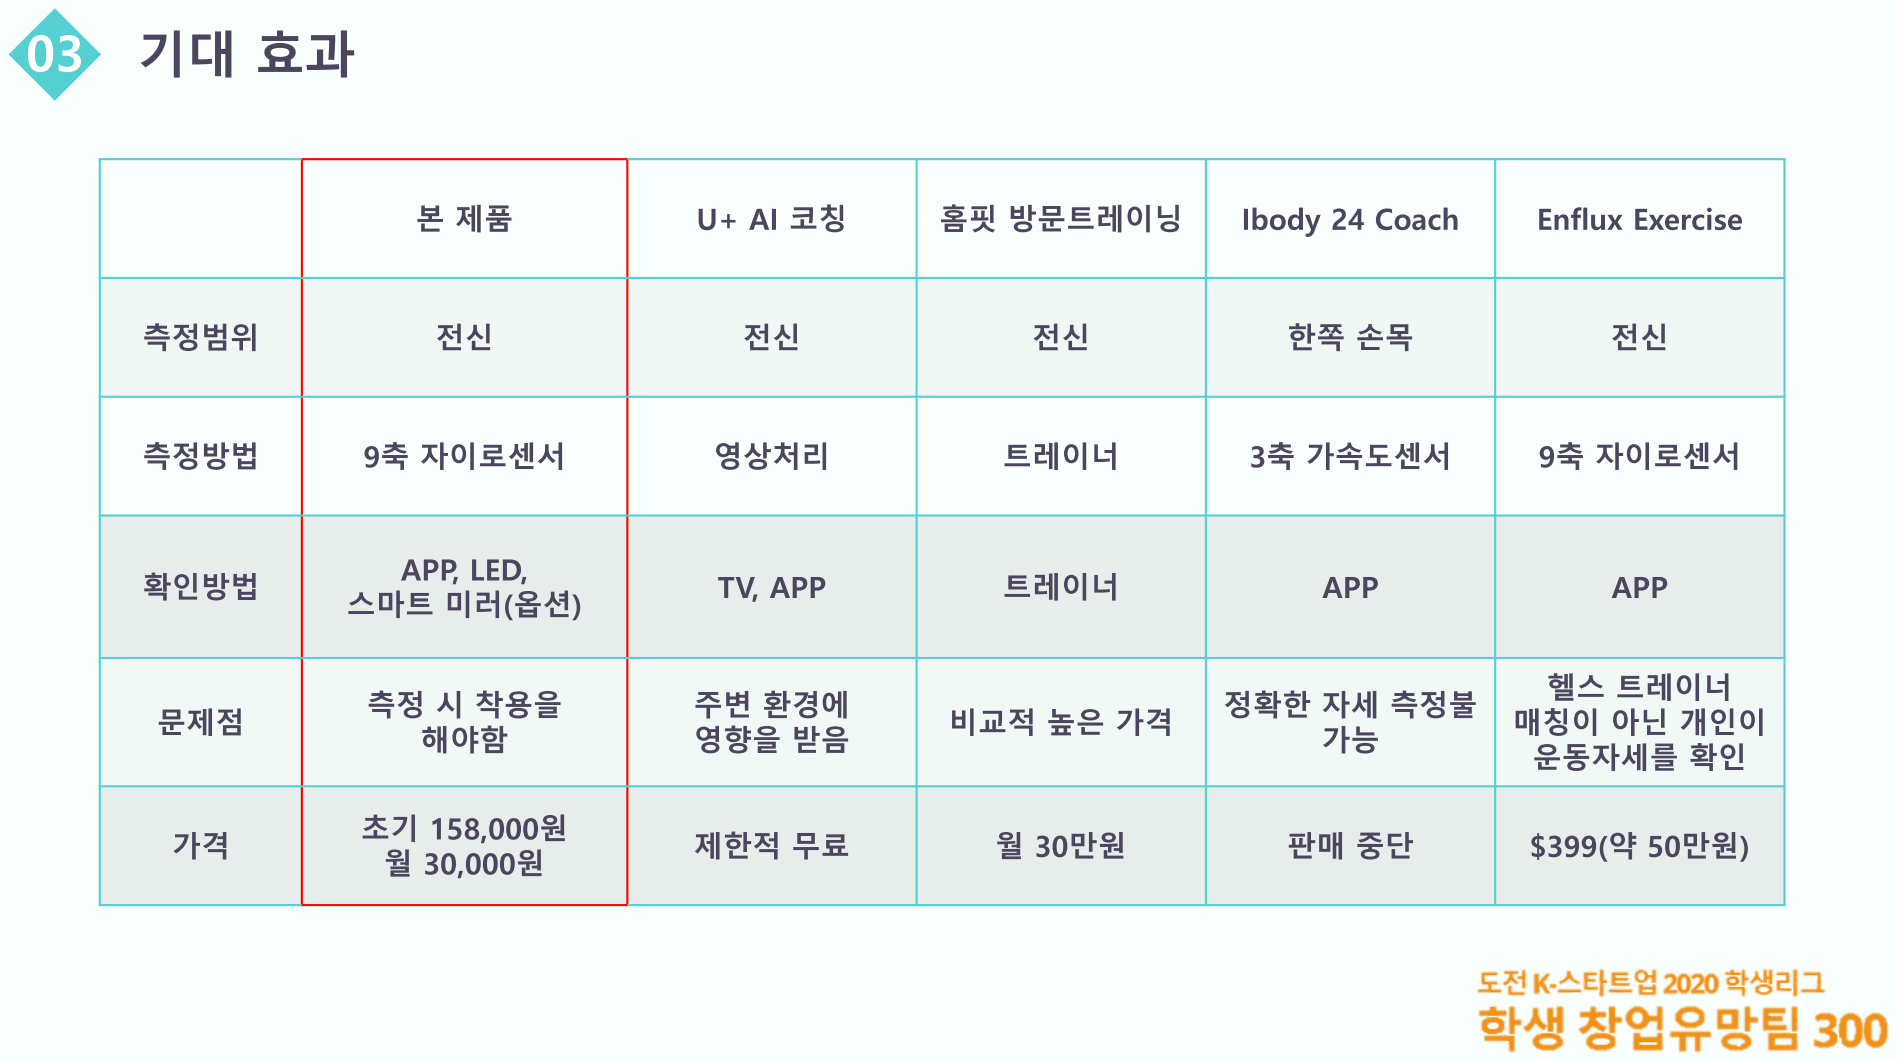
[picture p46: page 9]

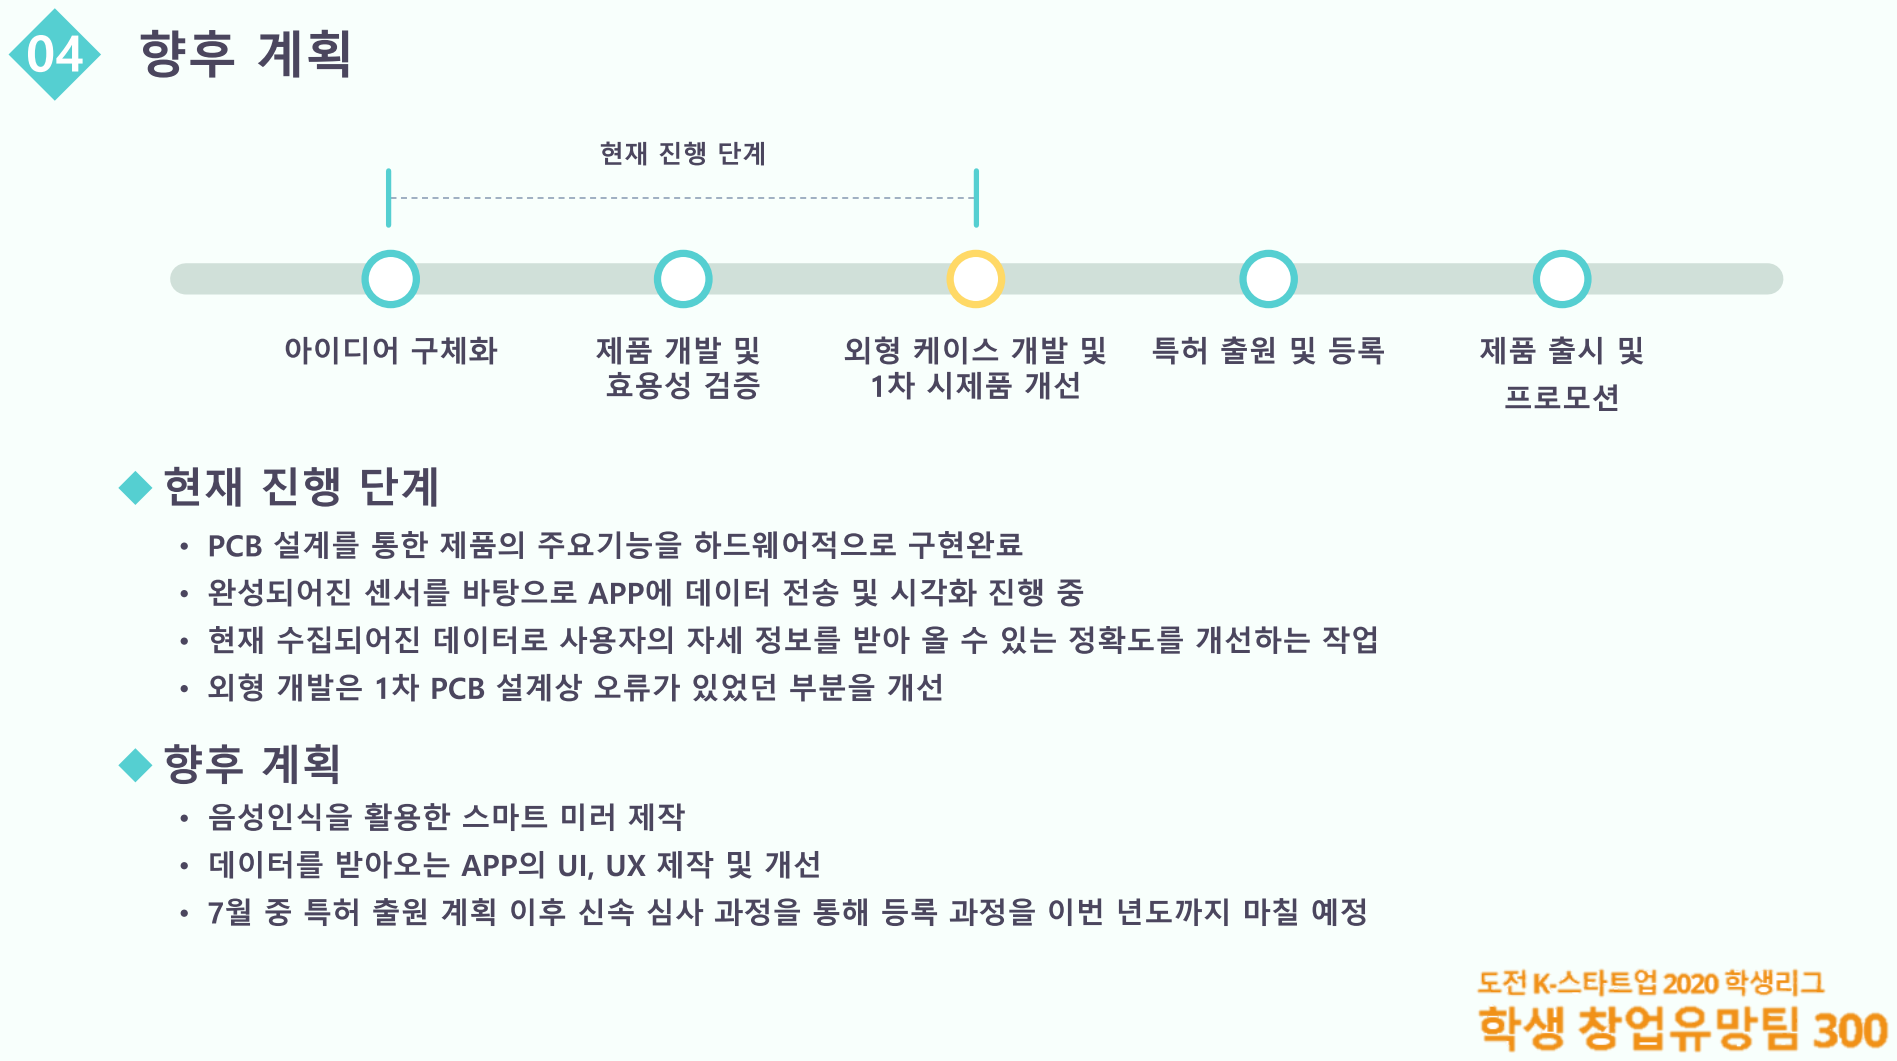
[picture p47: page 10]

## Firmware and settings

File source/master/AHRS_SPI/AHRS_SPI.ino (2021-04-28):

//MASTER
#include <SPI.h>
#include "MPU9250.h"
#include <esp_now.h>
#include <WiFi.h>
//#include "BluetoothSerial.h"

//BluetoothSerial bt;
#define RXD_RS485 33
#define TXD_RS485 25
#define RS485_E 26

int state;
int print_count;
int yaw_print[20];
int pitch_print[20];
int roll_print[20];
////////////////////////////////////////////////////////////////////////////////////////////////////////////////WiFi
uint8_t broadcastAddress[] = {0xFF, 0xFF, 0xFF, 0xFF, 0xFF, 0xFF};
char data_print[50];
char data_print_bt[50];

typedef struct struct_message {
    int id; // must be unique for each sender board
    float q0;
    float q1;
    float q2;
    float q3;
} struct_message;

//Create a struct_message called myData
struct_message myData;

// Create a structure to hold the readings from each board
struct_message board1;
struct_message board2;
struct_message board3;
struct_message board4;

// Create an array with all the structures
struct_message boardsStruct[4] = {board1, board2, board3, board4};

// callback when data is sent
void OnDataSent(const uint8_t *mac_addr, esp_now_send_status_t status) {
  Serial.print("\r\nLast Packet Send Status:\t");
  Serial.println(status == ESP_NOW_SEND_SUCCESS ? "Delivery Success" : "Delivery Fail");
}

// callback function that will be executed when data is received
void OnDataRecv(const uint8_t * mac_addr, const uint8_t *incomingData, int len) {
  memcpy(&myData, incomingData, sizeof(myData));
  digitalWrite(RS485_E, HIGH);
  print_count++;
  
  boardsStruct[myData.id-1].q0 = myData.q0;
  boardsStruct[myData.id-1].q1 = myData.q1;
  boardsStruct[myData.id-1].q2 = myData.q2;
  boardsStruct[myData.id-1].q3 = myData.q3;
  
  sprintf(data_print, "s%d%03d,%03d,%03d,%03d", myData.id, (int)(((boardsStruct[myData.id-1].q0)+1)*100), (int)(((boardsStruct[myData.id-1].q1)+1)*100), (int)(((boardsStruct[myData.id-1].q2)+1)*100), (int)(((boardsStruct[myData.id-1].q3)+1)*100));
  Serial.println(data_print);
  
  roll_print[myData.id] = atan2f(boardsStruct[myData.id-1].q0*boardsStruct[myData.id-1].q1 + boardsStruct[myData.id-1].q2*boardsStruct[myData.id-1].q3, 0.5f - boardsStruct[myData.id-1].q1*boardsStruct[myData.id-1].q1 - boardsStruct[myData.id-1].q2*boardsStruct[myData.id-1].q2) * 57.29578f;
  pitch_print[myData.id] = asinf(-2.0f * (boardsStruct[myData.id-1].q1*boardsStruct[myData.id-1].q3 - boardsStruct[myData.id-1].q0*boardsStruct[myData.id-1].q2)) * 57.29578f;
  yaw_print[myData.id] = atan2f(boardsStruct[myData.id-1].q1*boardsStruct[myData.id-1].q2 + boardsStruct[myData.id-1].q0*boardsStruct[myData.id-1].q3, 0.5f - boardsStruct[myData.id-1].q2*boardsStruct[myData.id-1].q2 - boardsStruct[myData.id-1].q3*boardsStruct[myData.id-1].q3) * 57.29578f + 180.0f;
  sprintf(data_print_bt, "s%03d,%03d,%03d,%03d,%03d,%03d", yaw_print[1]+500, pitch_print[1]+500, roll_print[1]+500, yaw_print[2]+500, pitch_print[2]+500, roll_print[2]+500);
  if(print_count == 5)
  {
    Serial1.println(data_print_bt);    
    Serial2.println(data_print_bt);
    print_count = 0;
  }

/*
  char macStr[18];
  Serial.print("Packet received from: ");
  snprintf(macStr, sizeof(macStr), "%02x:%02x:%02x:%02x:%02x:%02x",
           mac_addr[0], mac_addr[1], mac_addr[2], mac_addr[3], mac_addr[4], mac_addr[5]);
  Serial.println(macStr);
  memcpy(&myData, incomingData, sizeof(myData));
  Serial.printf("Board ID %u: %u bytes", myData.id, len);
  Serial.println();
  // Update the structures with the new incoming data

  boardsStruct[myData.id-1].q0 = myData.q0;
  boardsStruct[myData.id-1].q1 = myData.q1;
  boardsStruct[myData.id-1].q2 = myData.q2;
  boardsStruct[myData.id-1].q3 = myData.q3;
  Serial.print("q0 value: ");
  Serial.print(boardsStruct[myData.id-1].q0, 6);
  Serial.print(", ");
  Serial.print("q1 value: ");
  Serial.print(boardsStruct[myData.id-1].q1, 6);
  Serial.print(", ");  
  Serial.print("q2 value: ");
  Serial.print(boardsStruct[myData.id-1].q2, 6);
  Serial.print(", ");
  Serial.print("q3 value: ");
  Serial.print(boardsStruct[myData.id-1].q3, 6);
  Serial.println(); 
*/  
}
////////////////////////////////////////////////////////////////////////////////////////////////////////////////

//////////////////////////////////////////////////////////////////////////////////////////////////////////////Timer
/*
hw_timer_t * timer = NULL;
portMUX_TYPE timerMux = portMUX_INITIALIZER_UNLOCKED;

void IRAM_ATTR onTimer() {
  portENTER_CRITICAL_ISR(&timerMux);
  bt.println(data_print_bt);
  portEXIT_CRITICAL_ISR(&timerMux);
}
*/
//////////////////////////////////////////////////////////////////////////////////////////////////////////////


#define CHIP_SELECT_PIN         13

#define IMU_POLL_DELAY_MS         2
#define MFILTER_SAMPLE_FREQ_HZ    480
#define IMU_LOWPASSFILTER_BANDWIDTH   MPU9250::DLPF_BANDWIDTH_184HZ

#define CALIB_DISABLE
#define CALIB_DISABLE
//#define ACC_CALIB_DONE
//#define ACC_CALIB_Disable
//#define MAG_CALIB_DONE
#define MAG_CALIB_DISABLE

float q_value[3][4];
const byte gpio_input = 5;
int count;
#define RXD1 34
#define TXD1 32
//#define RXD1 11
//#define TXD1 34

#define ACC 0xF0
#define MAG 0xF1
#define GYRO 0xF2

String data_read;

int revision(float GYRO_X, float GYRO_Y, float GYRO_Z, float ACC_X_H, float ACC_X_L, float ACC_Y_H, float ACC_Y_L, float ACC_Z_H, float ACC_Z_L, float MAG_X_H, float MAG_X_L, float MAG_Y_H, float MAG_Y_L, float MAG_Z_H, float MAG_Z_L)
{
  unsigned long settime = millis();
  while(1)
  {
    Send_revision(GYRO, GYRO_X, GYRO_X, GYRO_Y, GYRO_Y, GYRO_Z, GYRO_Z);
    delay(50);
    Send_revision(ACC, ACC_X_H, ACC_X_L, ACC_Y_H, ACC_Y_L, ACC_Z_H, ACC_Z_L);
    delay(50);
    Send_revision(MAG, MAG_X_H, MAG_X_L, MAG_Y_H, MAG_Y_L, MAG_Z_H, MAG_Z_L);
    delay(50);
    if(((millis() - settime) > 5000)){
      return 1;
    }
  }  
}

void Send_revision(byte id, float X_H_data, float X_L_data, float Y_H_data, float Y_L_data, float Z_H_data, float Z_L_data)
{
  typedef struct revision_message {
      int id;
      float X_H;
      float X_L;
      float Y_H;
      float Y_L;
      float Z_H;
      float Z_L;
  } struct_message;
  revision_message myrevisionData;

  myrevisionData.id = id;
  myrevisionData.X_H = X_H_data;
  myrevisionData.X_L = X_L_data;
  myrevisionData.Y_H = Y_H_data;
  myrevisionData.Y_L = Y_L_data;
  myrevisionData.Z_H = Z_H_data;
  myrevisionData.Z_L = Z_L_data;
  esp_err_t result = esp_now_send(broadcastAddress, (uint8_t *) &myrevisionData, sizeof(myrevisionData));
  if (result == ESP_OK) {
    Serial.print(id);
    Serial.println(", Sent with success");
  }
  else {
    Serial.println("Error sending the data");
  }  
}

MPU9250 IMU(SPI, gpio_input);
Madgwick AHRSFilter;

int status;

typedef union {
  struct {
    float roll;
    float pitch;
    float yaw;
  };
  uint8_t valArray[sizeof(float) * 3];
} NotifBytesBunch;

NotifBytesBunch AHRSValues;

void setup() {
  Serial.begin(2000000);
  Serial1.begin(115200, SERIAL_8N1, RXD1, TXD1);
    Serial2.begin(115200, SERIAL_8N1, RXD_RS485, TXD_RS485);
//  bt.begin("ESP32_SIBAR");  

//  timer = timerBegin(0, 80, true);
//  timerAttachInterrupt(timer, &onTimer, true);
//  timerAlarmWrite(timer, 500000, true);  //1s = 1000000, 1ms = 10000 0.1ms = 10000 

  // Set device as a Wi-Fi Station
  WiFi.mode(WIFI_STA);

  // Init ESP-NOW
  if (esp_now_init() != ESP_OK) {
    Serial.println("Error initializing ESP-NOW");
    return;
  }
  
  // Once ESPNow is successfully Init, we will register for Send CB to
  // get the status of Trasnmitted packet
  esp_now_register_send_cb(OnDataSent);
  
  // Register peer
  esp_now_peer_info_t peerInfo;
  memcpy(peerInfo.peer_addr, broadcastAddress, 6);
  peerInfo.channel = 0;  
  peerInfo.encrypt = false;
  
  // Add peer
  if (esp_now_add_peer(&peerInfo) != ESP_OK){
    Serial.println("Failed to add peer");
    return;
  }
  pinMode(RS485_E, OUTPUT);
/*  
  while (!Serial) {}
  // start communication with IMU
  status = IMU.begin();
  if (status < 0) {
    Serial.println("IMU initialization unsuccessful");
    Serial.println("Check IMU wiring or try cycling power");
    Serial.print("Status: ");
    Serial.println(status);
    while (1) {}
  }

  IMU.setAccelRange(MPU9250::ACCEL_RANGE_16G);
  IMU.setGyroRange(MPU9250::GYRO_RANGE_2000DPS);
  IMU.setDlpfBandwidth(IMU_LOWPASSFILTER_BANDWIDTH);

  while (! Serial.available() ) {
      Serial.println("Start calibration");
      delay(10);
  }
   while (Serial.available() ) {
      Serial.read();    
      delay(5);
    }
  Serial.println(F("********** GYRO calib **************"));
  float gyrodir[3][3];
  for (uint8_t num = 0; num < 2; num++) {
    
    Serial.print(F("Don't move until I tell you.  "));
    Serial.print(num+1);
    Serial.println("...");  
    delay(500);
    state = IMU.calibrateGyro();
    if(state == 1){
      Serial.println(F("GYRO calib done"));
    }
    else{
      Serial.println(F("GYRO calib fail"));
    }
    Serial.println(F("Vals: "));
    Serial.print(F("X: "));
    gyrodir[0][num] = IMU.getGyroBiasX_rads();
    Serial.print(gyrodir[0][num], 6);
    Serial.println("rad/s");
    Serial.print(F("Y: "));
    gyrodir[1][num] = IMU.getGyroBiasY_rads();
    Serial.print(gyrodir[1][num], 6);
    Serial.println("rad/s");
    Serial.print(F("Z: "));
    gyrodir[2][num] = IMU.getGyroBiasZ_rads();
    Serial.print(gyrodir[2][num], 6);
    Serial.println("rad/s");
    if(num == 1){
      gyrodir[0][2] = (gyrodir[0][0] + gyrodir[0][1])/2;
      gyrodir[1][2] = (gyrodir[1][0] + gyrodir[1][1])/2;
      gyrodir[2][2] = (gyrodir[2][0] + gyrodir[2][1])/2;
      Serial.println(F("GYRO calib ALL done"));
      Serial.println(F("Vals: "));
      Serial.print(F("X: "));
      Serial.print(gyrodir[0][2], 6);
      Serial.println("rad/s");
      
      Serial.print(F("Y: "));
      Serial.print(gyrodir[1][2], 6);
      Serial.println("rad/s");
      
      Serial.print(F("Z: "));
      Serial.print(gyrodir[2][2], 6);      \
      Serial.println("rad/s");
      Serial.println();
      }
    }

  Serial.println(F("********** ACC calib **************"));
  float accdir[6][3];
  char * dirs[6] = { "X+", "X-", "Y+", "Y-", "Z+", "Z-"};

  for (uint8_t num = 0; num < 2; num++) {
      for (uint8_t i = 0; i < 6; i++) {
        Serial.print(F("Enter "));
        Serial.print((int)(num + 1));
        Serial.print(F(" when ready for dir "));
        Serial.print((int)(i + 1));
        Serial.print(' ');
        Serial.print(dirs[i]);
        while (! Serial.available() ) {
          delay(10);
        }
    
        while (Serial.available()) {
          Serial.read();
          delay(10);
          Serial.print('.');
        }
        Serial.println();
        state = IMU.calibrateAccel();
      }
      if(state == 1){
        Serial.println(F("Acc calib done"));
      }
      else{
        Serial.println(F("Acc calib fail"));        
      }
      Serial.println(F("Vals: "));
      Serial.print(F("X: "));
      accdir[0][num] = IMU.getAccelBiasX_mss();      
      Serial.print(IMU.getAccelBiasX_mss(), 6);
      Serial.print("m/s^2");
      Serial.print(" / ");
      accdir[1][num] = IMU.getAccelScaleFactorX();      
      Serial.print(IMU.getAccelScaleFactorX(), 6);
      Serial.println("m/s^2");
      Serial.print(F("Y: "));
      accdir[2][num] = IMU.getAccelBiasY_mss();
      Serial.print(IMU.getAccelBiasY_mss(), 6);
      Serial.print("m/s^2");      
      Serial.print(" / ");
      accdir[3][num] = IMU.getAccelScaleFactorY();      
      Serial.print(IMU.getAccelScaleFactorY(), 6);
      Serial.println("m/s^2");
      Serial.print(F("Z: "));
      accdir[4][num] = IMU.getAccelBiasZ_mss();
      Serial.print(IMU.getAccelBiasZ_mss(), 6);      
      Serial.print("m/s^2");
      Serial.print(" / ");
      accdir[5][num] = IMU.getAccelScaleFactorZ();      
      Serial.print(IMU.getAccelScaleFactorZ(), 6);
      Serial.println("m/s^2");      
      if(num == 1){
        accdir[0][2] = (accdir[0][0] + accdir[0][1])/2;
        accdir[1][2] = (accdir[1][0] + accdir[1][1])/2;
        accdir[2][2] = (accdir[2][0] + accdir[2][1])/2;
        accdir[3][2] = (accdir[3][0] + accdir[3][1])/2;
        accdir[4][2] = (accdir[4][0] + accdir[4][1])/2;
        accdir[5][2] = (accdir[5][0] + accdir[5][1])/2;
        
        Serial.println(F("Acc calib ALL done"));
        Serial.println(F("Vals: "));
        Serial.print(F("X: "));
        Serial.print(accdir[0][2], 6);
        Serial.print("m/s^2");
        Serial.print(" / ");
        Serial.print(accdir[1][2], 6);
        Serial.println("m/s^2");
        
        Serial.print(F("Y: "));
        Serial.print(accdir[2][2], 6);
        Serial.print("m/s^2");        
        Serial.print(" / ");
        Serial.print(accdir[3][2], 6);
        Serial.println("m/s^2");
        
        Serial.print(F("Z: "));
        Serial.print(accdir[4][2], 6);
        Serial.print("m/s^2");        
        Serial.print(" / ");
        Serial.print(accdir[5][2], 6);
        Serial.println("m/s^2");
        Serial.println();        
      }
  }

  Serial.println(F("********** MAG calib **************"));  
  float magdir[6][3];
  for (uint8_t num = 0; num < 2; num++) {
    Serial.print(F("CALIB MAG "));
    Serial.print((int)(num + 1));
    Serial.println(F(" -- move in figure 8s until I say stop!!! "));
    delay(500);
    state = IMU.calibrateMag();
    Serial.print((int)(num + 1));    
    if(state == 1){
        Serial.println(F("Mag calib done"));
    }
    else{
        Serial.println(F("Mag calib fail"));
    }
    Serial.println(F("Vals: "));    
    Serial.print(F("X: "));
    magdir[0][num] = IMU.getMagBiasX_uT();
    Serial.print(magdir[0][num], 6);
    Serial.print("uT");
    Serial.print(" / ");
    magdir[1][num] = IMU.getMagScaleFactorX();
    Serial.print(magdir[1][num], 6);
    Serial.println("uT");    
    Serial.print(F("Y: "));
    magdir[2][num] = IMU.getMagBiasY_uT();
    Serial.print(magdir[2][num], 6);
    Serial.print("uT");
    Serial.print(" / ");
    magdir[3][num] = IMU.getMagScaleFactorY();
    Serial.print(magdir[3][num], 6);
    Serial.println("uT");        
    Serial.print(F("Z: "));
    magdir[4][num] = IMU.getMagBiasZ_uT();
    Serial.print(magdir[4][num], 6);
    Serial.print("uT");
    Serial.print(" / ");
    magdir[5][num] = IMU.getMagScaleFactorZ();
    Serial.print(magdir[5][num], 6);
    Serial.println("uT");        
    if (num == 1) {
      magdir[0][2] = (magdir[0][0] + magdir[0][1]) / 2;
      magdir[1][2] = (magdir[1][0] + magdir[1][1]) / 2;
      magdir[2][2] = (magdir[2][0] + magdir[2][1]) / 2;
      magdir[3][2] = (magdir[3][0] + magdir[3][1]) / 2;
      magdir[4][2] = (magdir[4][0] + magdir[4][1]) / 2;
      magdir[5][2] = (magdir[5][0] + magdir[5][1]) / 2;
      Serial.println(F("Mag calib ALL done"));
      Serial.println(F("Vals: "));      
      Serial.print(F("X: "));
      Serial.print(magdir[0][2], 6);
      Serial.print("uT");
      Serial.print(" / ");
      Serial.print(magdir[1][2], 6);
      Serial.println("uT");          
      Serial.print(F("Y: "));
      Serial.print(magdir[2][2], 6);
      Serial.print("uT");
      Serial.print(" / ");
      Serial.print(magdir[3][2], 6);
      Serial.println("uT");          
      Serial.print(F("Z: "));
      Serial.print(magdir[4][2], 6);
      Serial.print("uT");
      Serial.print(" / ");
      Serial.print(magdir[5][2], 6);
      Serial.println("uT");          
    }
  }
  AHRSFilter.begin(MFILTER_SAMPLE_FREQ_HZ);

  IMU.setGyroBiasX_rads(gyrodir[0][2]);
  IMU.setGyroBiasY_rads(gyrodir[1][2]);
  IMU.setGyroBiasZ_rads(gyrodir[2][2]);

  IMU.setAccelCalX(accdir[0][2], accdir[1][2]);
  IMU.setAccelCalY(accdir[2][2], accdir[3][2]);
  IMU.setAccelCalZ(accdir[4][2], accdir[5][2]);
  
  IMU.setMagCalX(magdir[0][2], magdir[1][2]);
  IMU.setMagCalY(magdir[2][2], magdir[3][2]);
  IMU.setMagCalZ(magdir[4][2], magdir[5][2]);
//  revision(accdir[0][2], accdir[1][2], accdir[2][2], accdir[3][2], accdir[4][2], accdir[5][2], magdir[0][2], magdir[1][2], magdir[2][2], magdir[3][2], magdir[4][2], magdir[5][2]);
  revision(gyrodir[0][2], gyrodir[1][2], gyrodir[2][2], accdir[0][2], accdir[1][2], accdir[2][2], accdir[3][2], accdir[4][2], accdir[5][2], magdir[0][2], magdir[1][2], magdir[2][2], magdir[3][2], magdir[4][2], magdir[5][2]);
*/  
  esp_now_register_recv_cb(OnDataRecv);
//  timerAlarmEnable(timer);
}
float past_gx;
float past_gy;
float past_gz;

uint8_t loopCount = 0;
unsigned long ret_time;
void loop() {
  
}

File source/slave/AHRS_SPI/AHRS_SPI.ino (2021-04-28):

//SLAVE
#include <SPI.h>
#include "MPU9250.h"
#include <esp_now.h>
#include <WiFi.h>

#define CHIP_SELECT_PIN         13

#define IMU_POLL_DELAY_MS         2
#define MFILTER_SAMPLE_FREQ_HZ    480
#define IMU_LOWPASSFILTER_BANDWIDTH   MPU9250::DLPF_BANDWIDTH_184HZ

const byte gpio_input = 5;

int use_IMU = 2;

#define GYRO 0xF2
#define ACC 0xF0
#define MAG 0xF1

int count;
char data_print[50];

//////////////////////////////////////////////////////////////////////////////////////////////////////////WiFi
typedef struct struct_revision_message {
  int id;
  float X_H;
  float X_L;
  float Y_H;
  float Y_L;
  float Z_H;
  float Z_L;
}struct_revision_message;

// Create a struct_message called myData
struct_revision_message myData_revision;

//struct_revision_message board;
//struct_revision_message boardStruct[1] = {board};

void OnDataRecv_revision(const uint8_t * mac_addr, const uint8_t *incomingData, int len) {
  char macStr[18];
  memcpy(&myData_revision, incomingData, sizeof(myData_revision));  
}

// REPLACE WITH THE RECEIVER'S MAC Address
uint8_t broadcastAddress[] = {0xFF, 0xFF, 0xFF, 0xFF, 0xFF, 0xFF};

typedef struct struct_message {
    int id; // must be unique for each sender board
    float q0;
    float q1;
    float q2;
    float q3;
} struct_message;

//Create a struct_message called myData
struct_message myData;

// callback when data is sent
void OnDataSent(const uint8_t *mac_addr, esp_now_send_status_t status) {
  Serial.print("\r\nLast Packet Send Status:\t");
  Serial.println(status == ESP_NOW_SEND_SUCCESS ? "Delivery Success" : "Delivery Fail");
}
//////////////////////////////////////////////////////////////////////////////////////////////////////////

MPU9250 IMU(SPI, gpio_input);
Madgwick AHRSFilter;

int status;

typedef union {
  struct {
    float roll;
    float pitch;
    float yaw;
  };
  uint8_t valArray[sizeof(float) * 3];
} NotifBytesBunch;

NotifBytesBunch AHRSValues;

void setup() {
  Serial.begin(2000000);
  WiFi.mode(WIFI_STA);

  //Init ESP-NOW
  if (esp_now_init() != ESP_OK) {
    Serial.println("Error initializing ESP-NOW");
    return;
  }

  status = IMU.begin();
  if (status < 0) {
    Serial.println("IMU initialization unsuccessful");
    Serial.println("Check IMU wiring or try cycling power");
    Serial.print("Status: ");
    Serial.println(status);
    while (1) {}
  }

  IMU.setAccelRange(MPU9250::ACCEL_RANGE_16G);
  IMU.setGyroRange(MPU9250::GYRO_RANGE_2000DPS);
  IMU.setDlpfBandwidth(IMU_LOWPASSFILTER_BANDWIDTH);
  Serial.print("ID: ");
  Serial.println(use_IMU);
  Recive_revision();

  esp_now_register_send_cb(OnDataSent);  
  
  // Register peer
  esp_now_peer_info_t peerInfo;
  memcpy(peerInfo.peer_addr, broadcastAddress, 6);
  peerInfo.channel = 0;  
  peerInfo.encrypt = false;

  // Add peer
  if (esp_now_add_peer(&peerInfo) != ESP_OK){
    Serial.println("Failed to add peer");
    return;
  }
}

uint8_t loopCount = 0;

void loop() {
  IMU.readSensor(AHRSFilter);
  if (loopCount++ > 10) {
    loopCount = 0;
    float rolly = AHRSFilter.getRoll();
    if (rolly < 0) {
      // I like them positive
      rolly = 360.0 + rolly;
    }
    AHRSValues.roll = rolly;
    AHRSValues.pitch = AHRSFilter.getPitch();
    AHRSValues.yaw = AHRSFilter.getYaw();
    
    myData.id = use_IMU;
    myData.q0 =  AHRSFilter.getq0();
    myData.q1 = AHRSFilter.getq1();
    myData.q2 = AHRSFilter.getq2();
    myData.q3 = AHRSFilter.getq3();
    esp_err_t result = esp_now_send(broadcastAddress, (uint8_t *) &myData, sizeof(myData));
    if (result == ESP_OK) {
      Serial.println("Sent with success");
    }
    else {
      Serial.println("Error sending the data");
    }
  }
  delay(IMU_POLL_DELAY_MS);
}

int Recive_revision(void)
{
  int GYRO_CHECK = 0;
  int ACC_CHECK = 0;  
  int MAG_CHECK = 0;  
  esp_now_register_recv_cb(OnDataRecv_revision);
  while(1)
  {
    if((myData_revision.id == GYRO) && !GYRO_CHECK)
    {
      IMU.setGyroBiasX_rads(myData_revision.X_H);
      IMU.setGyroBiasY_rads(myData_revision.Y_H);
      IMU.setGyroBiasZ_rads(myData_revision.Z_H);
      Serial.println(F("********** GYRO **************"));
      Serial.println(F("Vals: "));
      Serial.print(F("X: "));
      Serial.print(myData_revision.X_H, 6);
      Serial.println("rad/s");
      Serial.print(F("Y: "));
      Serial.print(myData_revision.Y_H, 6);
      Serial.println("rad/s");
      Serial.print(F("Z: "));
      Serial.print(myData_revision.Z_H, 6);
      Serial.println("rad/s");
      Serial.println();
      GYRO_CHECK = 1;
    }
    else if((myData_revision.id == ACC) && !ACC_CHECK)
    {
      IMU.setAccelCalX(myData_revision.X_H, myData_revision.X_L);
      IMU.setAccelCalY(myData_revision.Y_H, myData_revision.Y_L);
      IMU.setAccelCalZ(myData_revision.Z_H, myData_revision.Z_L);
      Serial.println(F("********** ACC  **************"));
      Serial.println(F("Vals: "));
      Serial.print(F("X: "));
      Serial.print(myData_revision.X_H, 6);
      Serial.print("m/s^2");
      Serial.print(" / ");
      Serial.print(myData_revision.X_L, 6);
      Serial.println("m/s^2");
      Serial.print(F("Y: "));
      Serial.print(myData_revision.Y_H, 6);
      Serial.print("m/s^2");        
      Serial.print(" / ");
      Serial.print(myData_revision.Y_L, 6);
      Serial.println("m/s^2");
      Serial.print(F("Z: "));
      Serial.print(myData_revision.Z_H, 6);
      Serial.print("m/s^2");        
      Serial.print(" / ");
      Serial.print(myData_revision.Z_L, 6);
      Serial.println("m/s^2");
      Serial.println();
      ACC_CHECK = 1;
    }
    else if((myData_revision.id == MAG) && !MAG_CHECK)
    {
      IMU.setMagCalX(myData_revision.X_H, myData_revision.X_L);
      IMU.setMagCalY(myData_revision.Y_H, myData_revision.Y_L);
      IMU.setMagCalZ(myData_revision.Z_H, myData_revision.Z_L);
      Serial.println(F("********** MAG  **************"));        
      Serial.println(F("Vals: "));      
      Serial.print(F("X: "));
      Serial.print(myData_revision.X_H, 6);
      Serial.print("uT");
      Serial.print(" / ");
      Serial.print(myData_revision.X_L, 6);
      Serial.println("uT");          
      Serial.print(F("Y: "));
      Serial.print(myData_revision.Y_H, 6);
      Serial.print("uT");
      Serial.print(" / ");
      Serial.print(myData_revision.Y_L, 6);
      Serial.println("uT");          
      Serial.print(F("Z: "));
      Serial.print(myData_revision.Z_H, 6);
      Serial.print("uT");
      Serial.print(" / ");
      Serial.print(myData_revision.Z_L, 6);
      Serial.println("uT");             
      MAG_CHECK = 1;
    }
    if(GYRO_CHECK && ACC_CHECK && MAG_CHECK){
      return 1;
    }
  }
}

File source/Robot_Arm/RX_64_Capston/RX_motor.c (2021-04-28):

/*
 * RX_motor.c
 *
 * Created: 2020-08-29 오후 10:12:45
 *  Author: LEEHUIDO
 */ 
#define F_CPU 16000000UL
//#define RS485_TXD PORTE &= ~_BV(PE3),PORTE |= _BV(PE2)    		//_485_DIRECTION = 1

DDRF = 0b00000001;
//#define RS485_TXD	PORTF = 0b00000001;
//#define RS485_RXD	PORTF = 0b00000000;
#define RS485_TXD	PORTD |= 0b00010000;
#define RS485_RXD	PORTD &= 0b11101111;

#define sbi(REG8,BITNUM) REG8 |= _BV(BITNUM)

#include "RX_motor.h"
#include <avr/io.h>
#include <avr/interrupt.h>
#include <stdio.h>
#include <util/delay.h>

byte gbpTxBuffer[128];
byte gbpParameter[128];

void uart_mx_init(unsigned int ubrr)
{
	
	UBRR1H = (unsigned char)(ubrr>>8);    // Set baud rate
	UBRR1L = (unsigned char)ubrr;
	
	UCSR1A = 1<<U2X1;						// 비동기 2배속 모드 , U2X1==1
	UCSR1B = (1<<RXEN1) | (1<<TXEN1);		// Enable receiver and transmitter(송,수신 가능하게 함) , RXEN1==4  , TXEN1==3
	UCSR1C = 3<<UCSZ10;					// Set frame format: 8data, 1stop bit    ,   UCSZ10==1
}

void uart_mx_transmit(unsigned char data)
{
	while(!(UCSR1A & (1<<UDRE1)));		//UDRE1 = 5  , 레지스터 UCSR1A의 5비트는 자동(전송준비가 되면 1이된다)

	UDR1=data;
}

byte TxPacket_mx (byte bID,byte blnstruction,byte bParameterLength)	//ID값,Instruction,parameter 길이
{
	byte bCount,bCheckSum,bPacketLength;

	gbpTxBuffer[0] = 0xff;				//패킷의 시작을 알리는 신호
	gbpTxBuffer[1] = 0xff;				//패킷의 시작을 알리는 신호
	gbpTxBuffer[2] = bID;				//ID
	gbpTxBuffer[3] = bParameterLength+2;	//패킷의 길이  Instruction(1) + Parameter0(1) + ParameterN(N) Parameter 개수(N) + 2

	
	gbpTxBuffer[4] = blnstruction;		//Dynamixel에게 수행하라고 지시하는 명령.

	
	for(bCount = 0; bCount < bParameterLength; bCount++)		//Put gbpParameter Value in gbpTxBuffer
	{
		gbpTxBuffer[bCount+5] = gbpParameter[bCount];
	}

	bCheckSum = 0;
	bPacketLength = bParameterLength+6;			//StartByte(2) + IDByte(1) + LengthByte(1) + Instruction(1) + Parameter(1+N)

	for(bCount = 2; bCount<bPacketLength-1; bCount++)	//StartByte 제외, Parameter0 포함, CheckSum 계산
	{
		bCheckSum += gbpTxBuffer[bCount];
	}

	
	gbpTxBuffer[bCount] = ~bCheckSum;		// Check Sum = ~( ID + Length + Instruction + Parameter1 + … Parameter N )


	RS485_TXD
	_delay_ms(1);
	for(bCount=0;bCount<bPacketLength;bCount++)	//uart통신 Packet 전송
	{
		sbi(UCSR1A,6);
		uart_mx_transmit(gbpTxBuffer[bCount]);
	}
	while(!CHECK_TXD1_FINISH);		//전송이 끝날때 까지 대기
	RS485_RXD
	_delay_ms(1);	
	return(bPacketLength);		//Packet길이 반환
}

byte mx_ID(unsigned int ID_number)		//ID설정 함수
{
	gbpParameter[0] = 0x03;				//ID address
	gbpParameter[1] = ID_number;
	
	TxPacket_mx (0xFE,0x03,2);
}

byte mx_LED(unsigned int ID_number, unsigned int state)
{
	gbpParameter[0] = 0x19;				//ID address
	gbpParameter[1] = state;
	
	TxPacket_mx (ID_number,0x03,2);
}

byte mx_position(unsigned int p_number,unsigned int ID_number)			//모터 위치값,모터 ID값
{
	unsigned int position = 3.41*p_number;	//Change 0~300 to 0~1023
	gbpParameter[0] = 0x1E; //goal position(L) address
	gbpParameter[1] = (unsigned char)(position); //Writing Data  , goal position(L)
	gbpParameter[2] = (unsigned char)(position>>8); //goal position(H)

	TxPacket_mx (ID_number,0x03,3);	// , 0x03명령, 길이
}


void borate_set(unsigned int borate)		// 0x01 == 1M , 0x03 == 500000 , 0x04 == 400000 , 0x07 == 250000 , 0x09 == 200000  보레이트 변경하는 함수
{
	gbpParameter[0] = 0x04;		//Baud Rate Address
	gbpParameter[1] = borate; // 1M
	
	TxPacket_mx (0xFE,0x03,2); //모터 전체 , 0X03명령 , 길이
}


void All_Control_TEST(	unsigned int ID_number_1, int chose_1, unsigned int flexible_val_1,unsigned int flexible_1, unsigned int p_number_1, unsigned int AX_Speed_1,
unsigned int ID_number_2, int chose_2, unsigned int flexible_val_2,unsigned int flexible_2, unsigned int p_number_2, unsigned int AX_Speed_2,
unsigned int ID_number_3, int chose_3, unsigned int flexible_val_3,unsigned int flexible_3, unsigned int p_number_3, unsigned int AX_Speed_3,
unsigned int ID_number_4, int chose_4, unsigned int flexible_val_4,unsigned int flexible_4, unsigned int p_number_4, unsigned int AX_Speed_4,
unsigned int ID_number_5, int chose_5, unsigned int flexible_val_5,unsigned int flexible_5, unsigned int p_number_5, unsigned int AX_Speed_5)
{
	unsigned int position_1 = 3.41*p_number_1;			//Change 0~300 to 0~1023

	unsigned int position_2 = 3.41*p_number_2;			//Change 0~300 to 0~1023
	unsigned int position_2a = 3.41*(300-p_number_2);	//Change 0~300 to 0~1023

	unsigned int position_3 = 3.41*p_number_3;			//Change 0~300 to 0~1023
	unsigned int position_4 = 3.41*p_number_4;			//Change 0~300 to 0~1023
	unsigned int position_5 = 3.41*p_number_5;			//Change 0~300 to 0~1023

	unsigned int AX_Speed_5_c = 9*AX_Speed_5;
	unsigned int AX_Speed_4_c = 9*AX_Speed_4;
	unsigned int AX_Speed_3_c = 9*AX_Speed_3;
	unsigned int AX_Speed_2_c = 9*AX_Speed_2;
	unsigned int AX_Speed_1_c = 9*AX_Speed_1;
	
	int CheckSum_Value= 0;
	byte bCount,bCheckSum,bPacketLength;

	gbpTxBuffer[0] = 0xFF;
	gbpTxBuffer[1] = 0xFF;	//시작
	gbpTxBuffer[2] = 0xFE;	//ID

	gbpTxBuffer[3] = ((8 + 1)*5) + 4;	//길이 (L:Dynamixel별 Data Length, N:Dynamixel의 개수)

	gbpTxBuffer[4] = 0x83;	//명령

	gbpTxBuffer[5] =0x1a;
	gbpTxBuffer[6] =0x08;

	gbpTxBuffer[7] = 0x01;				//ID
	gbpTxBuffer[8] = flexible_val_1;	//유격 오차
	gbpTxBuffer[9] = flexible_val_1;	//유격 오차
	gbpTxBuffer[10] = flexible_1;		//유연성
	gbpTxBuffer[11] = flexible_1;		//유연성
	gbpTxBuffer[12] = (unsigned char)(position_1); //Writing Data  , goal position(L)
	gbpTxBuffer[13] = (unsigned char)(position_1>>8); //goal position(H)
	gbpTxBuffer[14] = (unsigned char)AX_Speed_1_c; //goal Speed(L)
	gbpTxBuffer[15] = (unsigned char)(AX_Speed_1_c >> 8); //goal Speed(H)

	gbpTxBuffer[16] = 0x02;				//ID
	gbpTxBuffer[17] = flexible_val_2;	//유격 오차
	gbpTxBuffer[18] = flexible_val_2;	//유격 오차
	gbpTxBuffer[19] = flexible_2;		//유연성
	gbpTxBuffer[20] = flexible_2;		//유연성
	gbpTxBuffer[21] = (unsigned char)(position_2); //Writing Data  , goal position(L)
	gbpTxBuffer[22] = (unsigned char)(position_2>>8); //goal position(H)
	gbpTxBuffer[23] = (unsigned char)AX_Speed_2_c; //goal Speed(L)
	gbpTxBuffer[24] = (unsigned char)(AX_Speed_2_c >> 8); //goal Speed(H)
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
